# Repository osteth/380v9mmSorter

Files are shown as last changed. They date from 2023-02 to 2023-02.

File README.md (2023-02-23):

# 380v9mmSorter
A 3D printed bullet casing sorter for separating 9mm from .380 

All printed parts were printed in polymaker PLA+ with 3 perimiters and 15% infill. I used the "organic" supports
in the latest alpha build of PrusaSlice https://github.com/prusa3d/PrusaSlicer/releases/  to avoid supports causing 
parts to have unnessesary roughness. 

I printed the main sorter body oriented upright with the face of the .380 outlet down on the build plate. 
This gave me the best print quality results. 

POC video - https://youtu.be/RARQG4GygJQ

This project is not in a tested nor final form, expect things to change as problems are identified and addressed. 

Here is a list of all of the non-printed parts I have used for this project:

Motor - https://www.amazon.com/gp/product/B07XMFLSPB/ref=ppx_yo_dt_b_search_asin_title?ie=UTF8&psc=1

Power Jack - https://www.amazon.com/gp/product/B08CMMQMP6/ref=ppx_yo_dt_b_asin_title_o03_s00?ie=UTF8&psc=1

Wire - https://www.amazon.com/gp/product/B07F111X9J/ref=ppx_yo_dt_b_asin_title_o04_s00?ie=UTF8&psc=1

Power adapter - https://www.amazon.com/gp/product/B08GCMJH31/ref=ppx_yo_dt_b_asin_title_o06_s01?ie=UTF8&psc=1

Power Switch - https://www.amazon.com/gp/product/B0BCV7V3RQ/ref=ppx_yo_dt_b_search_asin_title?ie=UTF8&th=1

Tenetive Addition:
RC car shock absorber - https://www.amazon.com/gp/product/B0BLC4NCK9/ref=ewc_pr_img_3?smid=AJ0RJEXY6CYX2&psc=1

I am experiencing an intermitant feed failure where the case does not fall in time and gets mashed by the plunger. 
I have ordered a couple of these shock absorbers to replace the crank shaft to see if I can remedy the failure by 
allowing the motor to complete its rotation by compressing the shock absorber I hope this will additionally prevent 
the machine from breaking itself or from deforming the jammed case. 

Please note that I made a decent effort to make things parametric and I definitly failed on the sorter body
but I redesigned the enclosure so that it is fully parametric to endusre that people could easily swap in 
different power jacks, buttons, etc. with ease. I built mine using all parts I had laying arround from other projects
and wanted to ensure that the greatest number of people could do the same. 

### Hardware
M3 hardware is used everywhere expect on the motor. M2 is used on the motor both for mounting and as a cross pin
 to hold the wheel to the motor shaft.

I used a flat washer on each side of the crank shaft to reduce friction and use a drop of locktite to 
keep the nut from walking itself off. maybe I can work on embedding a nylock nut and shoulder bolt or something
in the future but this is were its at now.

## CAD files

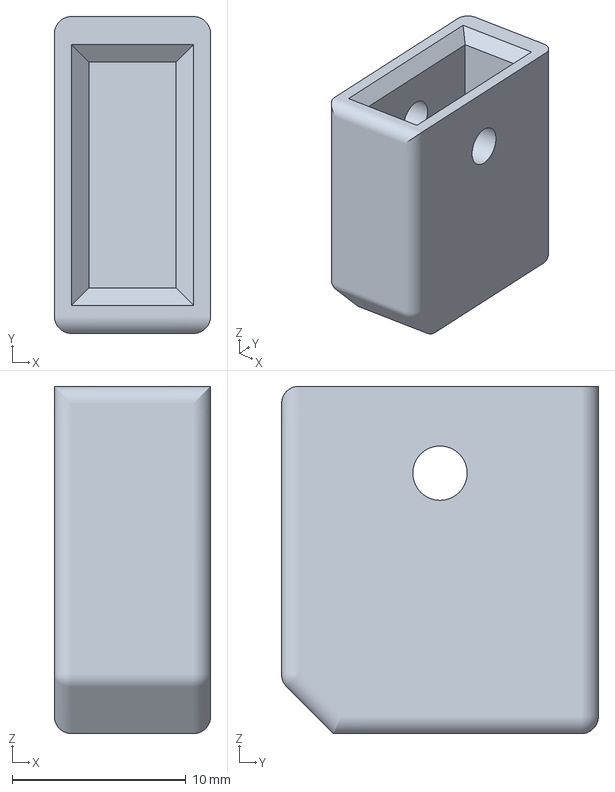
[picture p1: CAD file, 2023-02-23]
Prusa MK3S sliced Gcode/pusher.3mf
9.00 x 18.2 x 20.0 mm

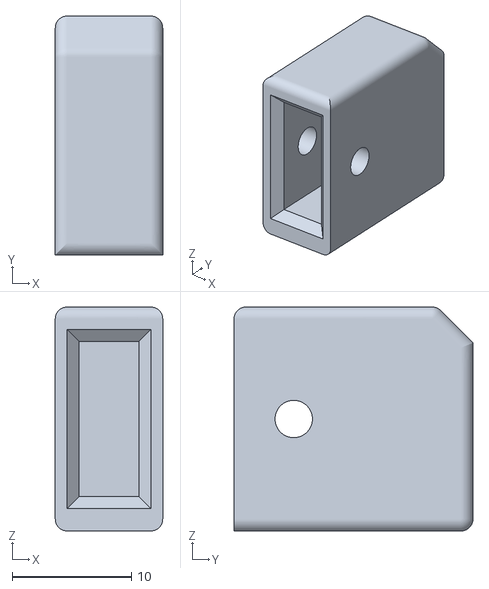
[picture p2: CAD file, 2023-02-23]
Pusher.stl
9.00 x 20.0 x 18.8

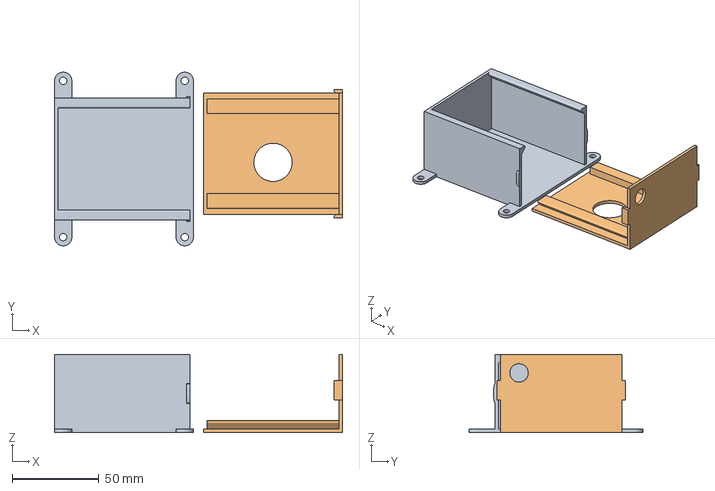
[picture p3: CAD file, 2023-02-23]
Prusa MK3S sliced Gcode/Enclosure.3mf
165.8 x 100.0 x 45.0 mm
Enclosure Body.stl
Enclosure Lid.stl

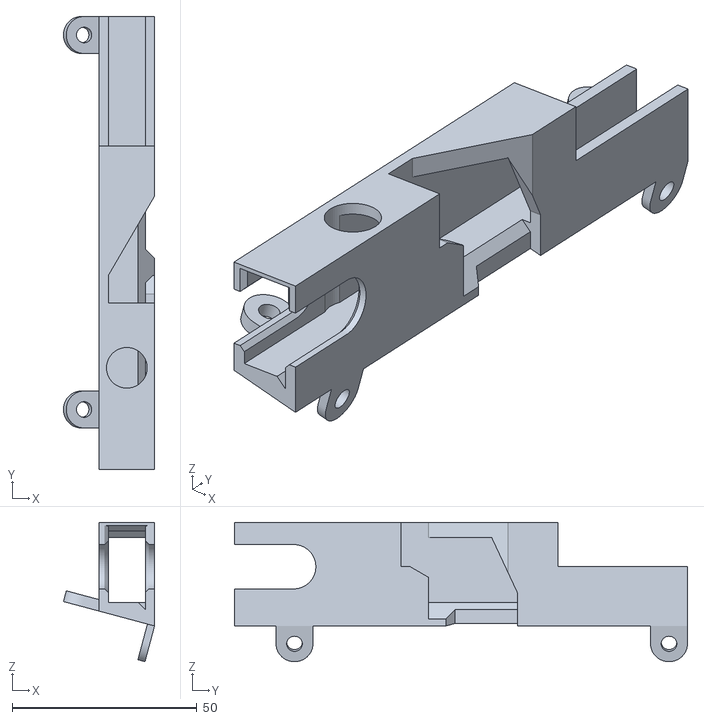
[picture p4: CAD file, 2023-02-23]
sorter_body.stl
24.7 x 122.5 x 37.7

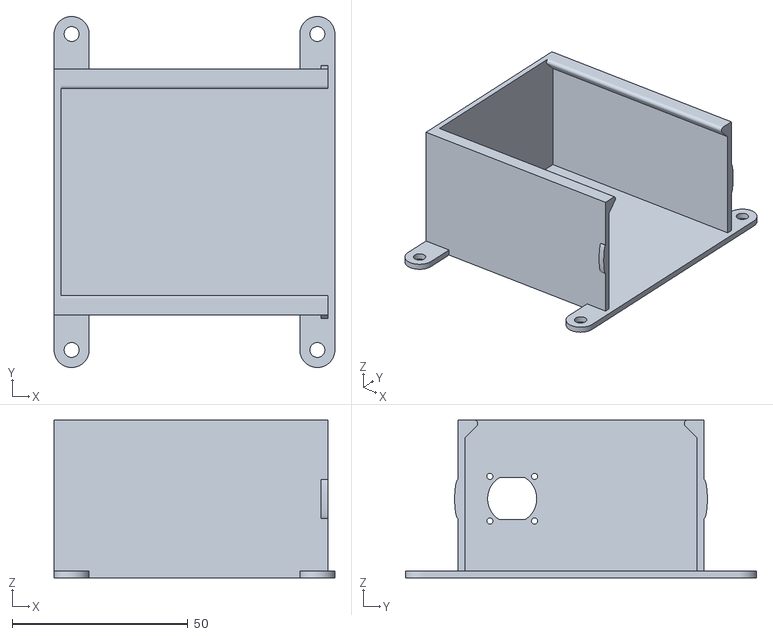
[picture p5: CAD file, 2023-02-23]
Enclosure Body.stl
80.0 x 100.0 x 45.0

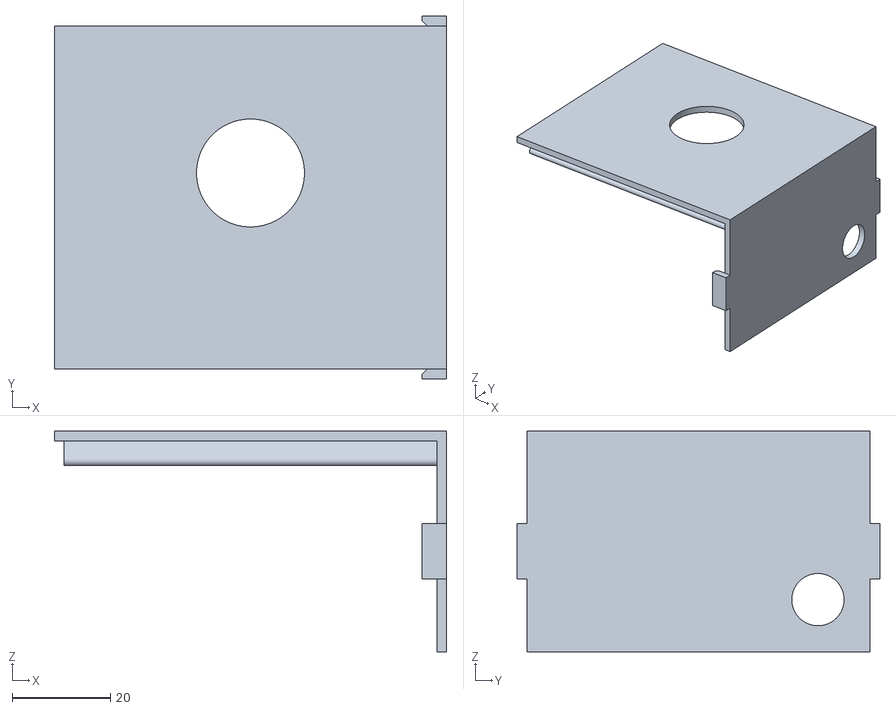
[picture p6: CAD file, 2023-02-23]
Enclosure Lid.stl
80.0 x 74.0 x 45.0

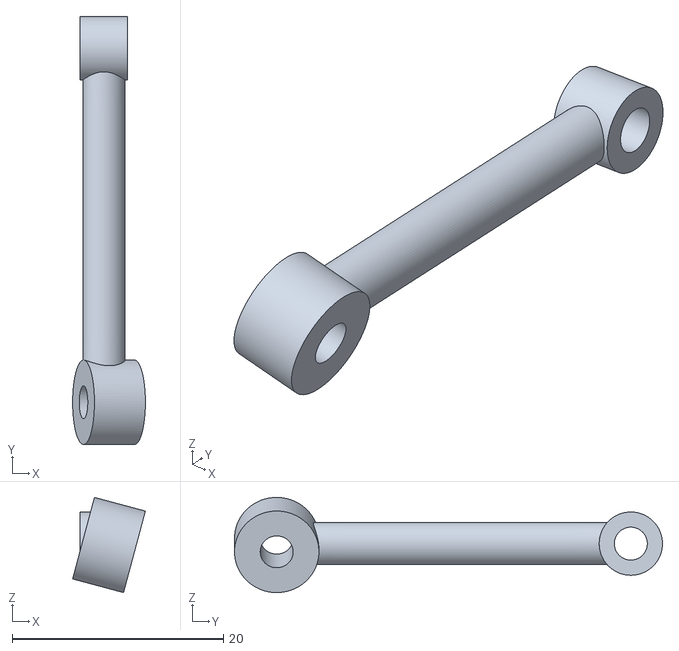
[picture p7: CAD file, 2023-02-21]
crank_shaft.stl
6.90 x 40.6 x 9.02

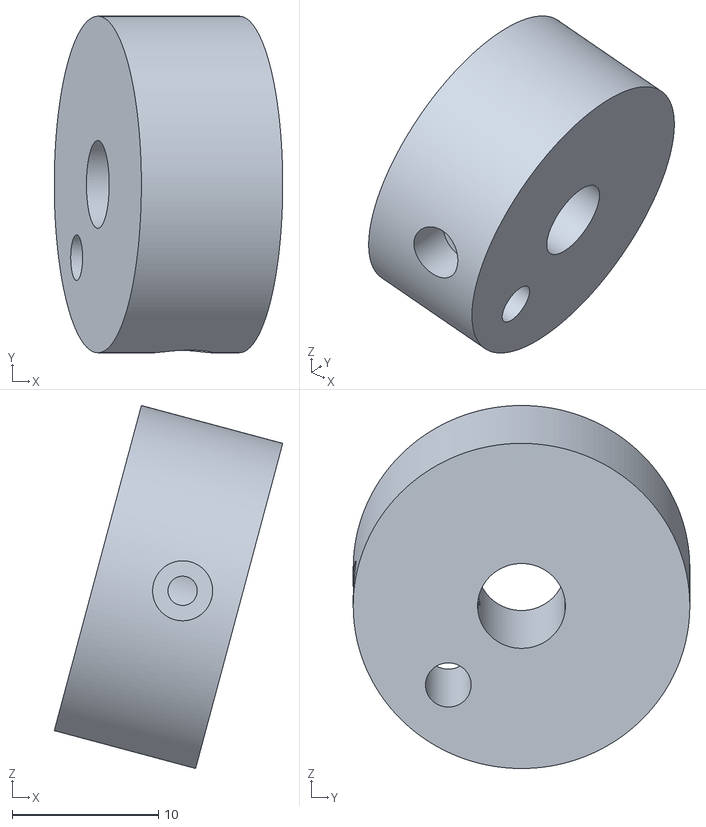
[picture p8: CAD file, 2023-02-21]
flywheel.stl
15.6 x 23.0 x 24.8

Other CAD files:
Prusa MK3S sliced Gcode/sorter_body.3mf
380 vs 9mm Sorter v4.f3z
Sorter enclosure v5.f3z
Sorter no flip v10.f3z

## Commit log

2023-02-21 Initial release
    Release of the first working proof of concept build.
    [Enclosure_lid.stl, Sorter no flip v10.f3z, crank_shaft.stl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]
2023-02-23 Alpha Release
    I have iterated and tested each part multiple times with positive results. I believe the current iteration is ready for additional people to test and ensure that it is widely replicable.
    [380 vs 9mm Sorter v4.f3z, Enclosure Body.stl, Enclosure Lid.stl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]
